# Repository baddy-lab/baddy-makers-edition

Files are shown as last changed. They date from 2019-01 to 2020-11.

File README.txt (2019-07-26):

    .__        ___       _______   _______  ____    ____
|   _  \      /   \     |       \ |       \ \   \  /   /
|  |_)  |    /  ^  \    |  .--.  ||  .--.  | \   \/   /
|   _  <    /  /_\  \   |  |  |  ||  |  |  |  \_    _/
|  |_)  |  /  _____  \  |  '--'  ||  '--'  |    |  |
|______/  /__/     \__\ |_______/ |_______/     |__|

Copyright Benoit GRESLEBIN 2018.
This documentation describes Open Hardware and is licensed under the
CERN OHL v. 1.1.  You may redistribute and modify this documentation
under the terms of the CERN OHL v.1.1. (http://ohwr.org/cernohl). This
documentation is distributed WITHOUT ANY EXPRESS OR IMPLIED WARRANTY,
INCLUDING OF MERCHANTABILITY, SATISFACTORY QUALITY AND FITNESS FOR A
PARTICULAR PURPOSE. Please see the CERN OHL v.1.1 for applicable conditions

######################################
ADDITIONAL TERMS
######################################
Specific non commercial use term: This source Hardware plan may be copied, distributed, modified by any individual
and non profit organizations (Fablab, Hackerspaces, Makerspaces, universities, Schools), as long
as it follows the CERN OHL V1.1 license terms here attached.
Corporate institutions and private companies may only copy and distribute the Hardware plan without modification.
Therefore, they are not allowed to modify the Hardware plan prior to distributing it for commercial purpose.
So for example, if a user embeds or modifies or relies on the Hardware plan in a product that is
then sold to a third party, this would be a violation of the Non-Commercial Use License additional term. 
By adding this additional restriction, it is intended to encourage the evolution of BADDY Hardware plan 
and design to be driven by the Hacker and makers' communities.

######################################
CONTRIBUTORS
######################################
Any change to be proposed on this gitlab, or at contact@baddy.space

######################################
PRODUCTS AND DISTRIBUTORS
######################################
Any intent of commercial use (selling BADDY Hardware DIY Kits and add-ons, not services around BADDY) to be notified to contact@baddy.space

######################################
CHANGE LOG - HISTORY
######################################

February 2018 - First open release
November 2018 - New git lab using Electrolab environment
January 2019 - New git public repository on GitHub

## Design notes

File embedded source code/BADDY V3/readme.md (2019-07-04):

In order to install BADDY new firmware, you need:
- To install VScode with PlatformIO modules installed. Once VS code installed, install the PlatformIO add-on with it's C/C++ extensions
- Take and Android cable (data transferred enabled) to connect your BADDY to your laptop (mac or PC)
- Note that OTA update available (to BADDY WiFi network) and uncomment the lines with ";" int the platformio.ini file.

The libraries that need to be installed:
- ArduinoJson by Benoit Blanchon
- LedControl by Eberhard Fahle
- AsyncTCP and ESPAsynTCP by Hristo Gochkov
- mDNSResolver by Myles Eftos

Once main.cpp, platformini.io and libraries installed and ready, please build project and upload and monitor to check logs

For any question, please join BADDY Facebook Group - there is a dedicated discussion Group on Firmware updates

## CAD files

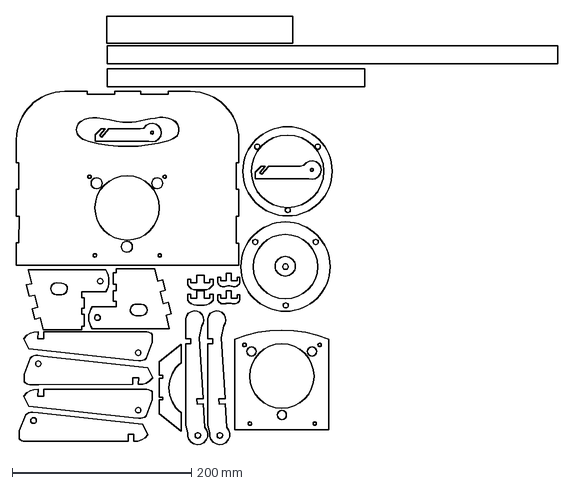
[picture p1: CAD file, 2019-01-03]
lasercut parts - mechanics and box/BADDY V1 DIY - 6mm.dxf
604.5 x 479.3 mm

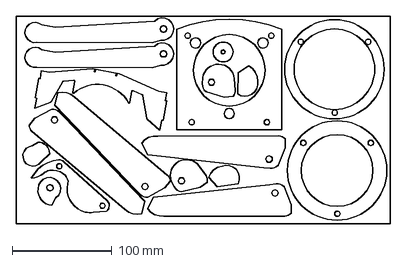
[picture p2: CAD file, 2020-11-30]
lasercut parts - mechanics and box/box v3/BADDY 6mm PMMA.dxf
375.2 x 207.9 mm

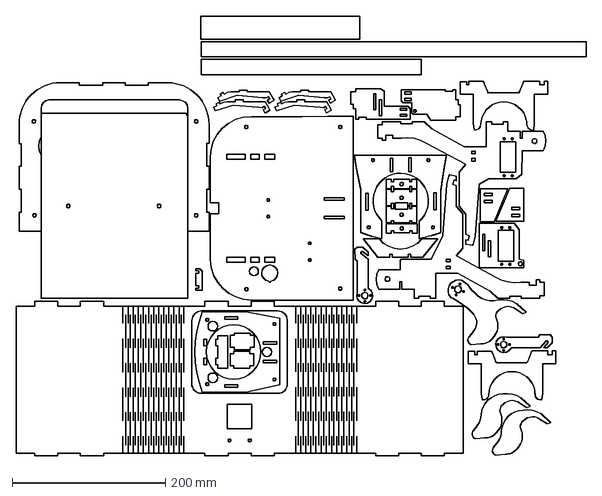
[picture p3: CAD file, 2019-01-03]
lasercut parts - mechanics and box/BADDY V1 DIY - 3mm.dxf
745.1 x 574.3 mm

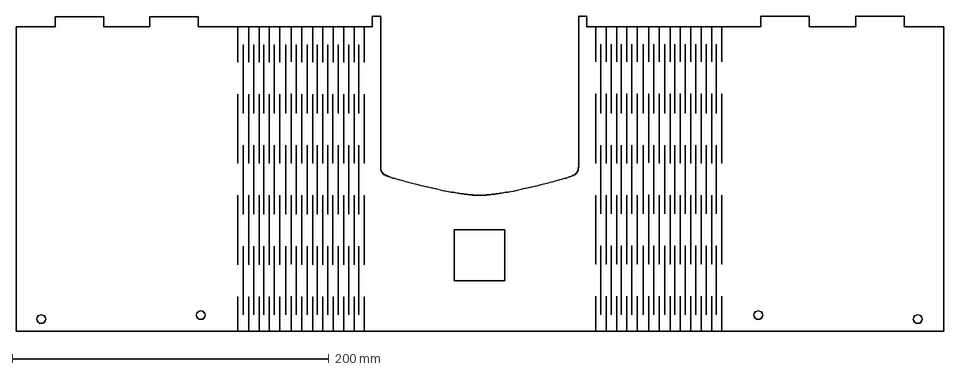
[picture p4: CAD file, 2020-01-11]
lasercut parts - mechanics and box/box v3/3mm front mdf.dxf
585.1 x 199.0 mm

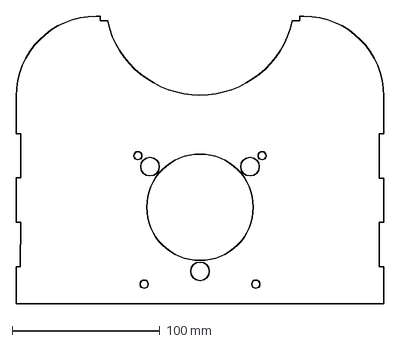
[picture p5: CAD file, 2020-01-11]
lasercut parts - mechanics and box/box v3/6mm top mdf.dxf
248.5 x 194.3 mm

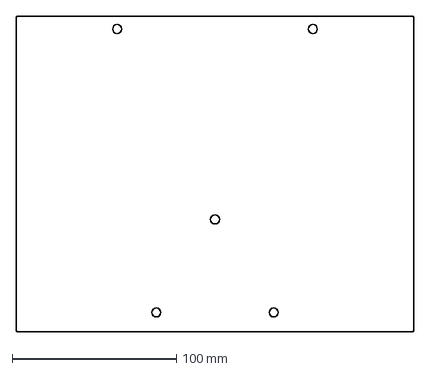
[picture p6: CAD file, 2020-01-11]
lasercut parts - mechanics and box/box v3/3mm back mdf.dxf
242.0 x 192.0 mm

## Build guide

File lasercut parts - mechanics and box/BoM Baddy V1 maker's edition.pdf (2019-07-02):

Groups | Mounting Steps | Video tutorial + Photo reference | Reference | Description | Quantity | Size | Comments
| 1 | | | Baddy box | 5 | | 5 units of glued wood or plexisglass
| | | BADDY BOX PL3 001 | Box front | 1
| | | BADDY BOX PL6 002 | Box top | 1
| | | BADDY BOX PL3 003 | Box bottom | 1
| | | BADDY BOX PL3 004 | Box lid | 1
| | | BADDY BOX PL6 005 | Box tube magnet cap | 1
| 2 | | | Baddy feeder | 3
| | | BADDY TUB PL3 006 | Tube | 1 | | Transparent tube diameter : 80 / 74mm ; height : 61 cm
| | | BADDY TUB PL6 007 | Tube lower collar | 1
| | | BADDY TUB PL6 008 | Tube upper collar | 1
| | | | Feeder screw | 3 | M6X18 | 3 Chc screwswith collar 6
| 3 | | | Baddy frame | 4 | | 4 glued units
| | | BADDY FRA PL3 009 | Frame lower board | 1
| | | BADDY FRA PL6 010 | Frame right side | 1
| | | BADDY FRA PL3 011 | Frame left side | 1
| | | BADDY FRA PL3 012 | Frame upper board | 1 | | In wood
| 4 | | | Baddy Firebox | 22 | | 22 glued units
| | | BADDY CHA PL3 013 | Firebox right side | 1
| | | BADDY CHA PL3 014 | Firebox left side | 1
| | | BADDY CHA PL3 015 | Firebox front assembly cleat | 1
| | | BADDY CHA PL3 016 | Firebox back cleat | 2
| | | BADDY CHA PL3 017 | Firebox upper board | 1
| | | BADDY CHA PL3 018 | Firebox magnet board | 1
| | | BADDY CHA PL3 019 | Firebox second right side | 1
| | | BADDY CHA PL3 020 | Firebox second left side | 1
| | | BADDY CHA PL6 021 | Firebox upper retainer neck | 1
| | | BADDY CHA PL3 022 | Firebox lower retainer neck | 1
| | | BADDY CHA PL3 023 | Firebox flange | 4
| | | BADDY CHA PL3 024 | Firebox wing | 2
| | | BADDY CHA PL3 025 | Firebox servo-motor board | 1
| | | BADDY CHA PL3 026 | Firebox spacer | 2
| | | BADDY CHA PL3 027 | Firebox servo-motor support | 1
| | | BADDY CHA PL3 028 | Firebox shuttle holder | 1
| 5 | | | Baddy shuttle retainer | 6 | | 3 glued units
| | | BADDY CHA PL3 029 | Firebox retainer | 2 | | 1 added part
| | | BADDY CHA PL3 030 | Firebox right arm | 2 | | 1 added part
| | | BADDY CHA PL6 031 | Firebox left arm | 2 | | 1 added part
| 6 | | | Baddy shuttle switch | 3 | | 3 glued units
| | | BADDY CHA PL3 032 | Firebox central switch | 1
| | | BADDY CHA PL3 033 | Firebox side switch | 2
| 7 | | | Front foot | 6 | | 6 glued units
| | | BADDY FRA PL6 034 | Baddy frame front foot | 4
| | | BADDY FRA PL6 035 | Baddy frame front foot cleat | 2
| | | | Rear foot | 5 | | 4 glued units
| | | BADDY FRA PL6 036 | Baddy frame rear foot | 2
| | | BADDY FRA PL6 037 | Baddy frame rear foot cleat | 2
| | | BADDY FRA PL6 038 | Baddy frame rear foot washer | 1 | | Thickness : 6 cm

BADDY
Structure

End of glued operations

Electronics +
Motors
8 | BADDY FRA 3D8 039 | Tripod holder | 1 | | 3D unit
| | Tripod holder bolt | 2 | M3x12 | 2 countersunk head screws + 2nylstop nuts
9 | BADDY CHA ELE 040 | Switch and retainer servo-motors | 2 | | H-KING HK 15298
| | Servo-motor bolt | 8 | M2,5x12 | 8 Chc screws + 8 nylstop nuts
10 | BADDY FRA ELE 041 | Motors | 2 | | 5,5V / 3A with ESC, beam and donkey
| | Motor bolt | 8 | M4x20 | 8 Chc screws + 8 nylstop nuts
| | Rubber washer | 16 | 4 – 9 | 16 ruber washers
| | Washer | 16 | 4 – 10 | 16 washers
11 | BADDY BOX ELE 042 | PCB 6 8X8 display beam (Led Square) | 1 | | 8X8 display – PCB card + 5 pinheader beam
| BADDY BOX WO3 043 | Baddy identity plate | 1 | | Fixed on Baddy box with 8X8 display
| | 8x8 display spacer | 2 | 3 – 7 – 6 | 2 spacers length : 6
| | 8x8 display bolt | 2 | M3x20 | 2 Chc screws + 2 nylstop nuts
12 | | Electronic card | 3 | | 2 units to pin on 1 Baddy PCB
| BADDY FRA ELE 044 | PCB card | 1
| BADDY FRA ELE 045 | Nano Arduino | 1 | | Pin on PCB card
| BADDY FRA ELE 046 | Bluetooth card | 1 | | Pin on PCB card
| | Electronic card spacer | 2 | 3 - 7 - 8 | 2 spacers length : 6
| | Electronic card bolt | 2 | M3x16 | 2 Chc screws + 2 nylstop nuts
13 | BADDY FRA ELE 047 | Switch on/off | 1 | | 1 unit to clip on Baddy lower frame
14 | BADDY FRA ELE 048 | Battery block | 1 | | PM-12V 6800mAh-CLIB ; battery beam to plug with main beam
15 | BADDY FRA ELE 049 | Main electric beam | 1 | | Motors - switch on/off – battery block
16 | | Assembly shuttle Firebox on Baddy frame front bolt | 1 | M4x20 | 1 Chc screw + 1 nylstop nut + 1 washer
Note: motor wire and servo-motors shall be wired to PCB Battery shall be connected to electric beam

Important: Before going to next step, please power on to initialize servo-motors position

Internal parts assembly | 17 | | Pulley on servo-motor | 2 | | Pulleys provided with servo-motors (drill 4 holes : 2 mm)
| | | Shuttle switch pulley bolt | 4 | M2x8 | 4 Chc screws + 4 nylstop nuts
| | | Shuttle retainer pulley bolt | 4 | M2x8 | 4 Chc screws + 4 nylstop nuts
| | | Shuttle retainer bolt on shuttle Firebox | 1 | M3x16 | 1 Chc screw + 1 nylstop nut + 3 washers
| | | Pulley on servo-motor screw | 2 | M3X7 | Provided with servo-motors
| 18 | BADDY FRA ELE 050 | Baddy wheel hub | 2 | | Assembly on wheels
| | | Wheel hub bolt | 8 | M3X10 | 8 Chc screws + 8 nylstop nuts
| | BADDY FRA ELE 051 | Baddy wheel | 2 | | Assembly on motors (allen key provided with the hub)
| 19 | BADDY BOX MAG 052 | Magnet | 3 | | Power : 10 daN
| 20 | | Assembly shuttle Firebox on Baddy box bolt | 4 | M3x25 | 4 Chc screws + 4 nylstop nuts
| 21 | | Assembly Baddy frame on Baddy box bolt | 4 | M4x12 | 4 Chc screws + 4 nylstop nuts

Connection 8X8 Led Square (Display Beam) to electronic card

End of assembly Baddy frame on Baddy box

External parts assembly | 22 | | Lid | 1 | | Assembly on shuttle firebox closing the Baddybox
| | | Rear lid pinched nut | 2 | | 2 pinched nuts
| | | Rear lid screw | 2 | M4x16 | 2 Chc screws
| | | Baddy box feet
| | | Front foot bolt | 2 | M6X30 | 2 Chc screws + 2 nylstop nuts + 12 washers
| | | Rear foot bolt | 1 | M6X34 | 1 Chc screw + 1 nylstop nut + 4 washers + rear foot washer 6cm
| 23 | BADDY BOX ELE 053 | USB cable | 1
| 24 | BADDY BOX TRI 054 | Tripod adapter | 1
| 25 | BADDY BOX ELE 055 | Battery charger | 1

## OPERATING BADDY

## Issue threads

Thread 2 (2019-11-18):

Wheels missing?

gistol, 2019-11-18:
Hi. Can you share some CAD files or .svg vector files for the wheels?

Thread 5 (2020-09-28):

Implicit assumptions

gvghia, 2020-09-28:
The program is full of assumptions and because they are not asserted, the controller can easily get into trouble.
The assumptions are that the positions to play are fixed and that there is a range of speeds attached to it.
The adjusting of motor speeds is based on these assumptions, which is so bad programming.
It is also limiting the uses of the Baddy.

What should be done in the speedadjuster is that the entered speeds are compared and not the programmed types. Based on the difference, some intermediate speed steps are to be done or not. For one step, the intermediate speed could be calculated as  the average of the actual running speed and the target speed. With a negative difference, you can decide to break or not, to reduce speed.

I'm talking about int motor_speed_transition(int type, int next_type){
From the types you get the programmed speeds: speed and next_speed for each motor.
With these  speeds you do the necessary adjustments by calling for each motor:
 int motor_speed_adjust(int motor, int speed, int next_speed){
if speed == next_speed return
if speed - next_speed > brake_step do_some_breaking(motor, speed, next_speed)
if next_speed - speed > acceleration_step do_some_acceleration(motor, speed, next_speed)
set_speed(motor, next_speed)
return

This simplifies the program a lot, because all type transistions use the same routine.

It will avoid unadapted speed transitions, when the implicit assumptions are not there.

Because the transistions are based on the required speeds, the speed adjustment is smoother.

It enlarge the possibilities in the training strokes of Baddy.
For example: we train youth players and operate Baddy, at the same side of the net as Baddy. As we face also the net, it is a mirrored view as the player who operates Baddy himself.
For easy programming, and having the same terrain view on the screen of the app, it makes sense to switch drop and clear by reversing the higher and lower speeds.
Also when I want the 9 training points on a line, or reduce the surface of the 9 point square to eg the backhand rear, or  ...
In both these cases, the controller is inducing contraproductive speed steps, which make these modes of operation almost impossible.

We are also looking out for more saved settings, (10?) in addition of the 2 existing, ground and tripod settings, preferably named, as we train also for Minibad, which uses only half of a field and therefore need settings to cover a narower surface.

baddy-team, 2020-11-11:
Hello! Thanks for reviewing the code. Yes, functions need to be updated, especially this one, that needs some cleaning and enables more dynamic configurability. We initially wanted something generic, but here comes the reality of the field experience, and in our context, these are 2 structuring points to bear in mind (among others not listed below), which led to this current versions with static exceptions:

- We cannot control Acceleration curves on ESCs, we just input speeds values to ESCs. That means we can't really control the time frame when an ESC will change from speed A to speed B
- We have to cope with batteries burst capabilities (ESCs may ask for 20A at full burst) which can block the battery

Given the 2 structuring points above, the situation is getting actually a bit more tricky than expected, and had finally to configure for each combination speed A to speed B, the most accurate speeds changes (mainly static considerations, yes).

That doesn't mean it's not possible to rewrite it, it's rather a must (like many other parts of BADDY code). But let's be careful to test it accurately before releasing anything, since this function actually impacts the functioning of the robot, in solo and buddy mode.

So, don't hesitate to push a proposal and I guess a lot of members will be glad to test and experience with you (we will thoroughly test any update before release).

We keep in touch!

gvghia, 2020-11-12:
Hi,

I want to suggest the varspeedservo [3] library.

Not tested myself, but it seems very easy to change the speeds in an
acceleration manner.
I think it will take some experiments to find an optimum between time
and current drawn.
It seems you can read back [4] the value and thus know if the speed
(programaticaly) is atteint.

I think this will simplify a lot the speed settings.

Other measures may be extended separate buffering of the 12v supply to
the Arduino. (eg 12 V - 10 ohm - 5000 uF - supply Arduino)

Another suggestion is a function that the front display indicates the
positon of the next trow.  Of course it is switchable, so random can
still be unexpected!

Regards,

Gerard Vanderveken

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

Links:
------
[1]
https://github.com/baddy-lab/baddy-makers-edition/issues/5#issuecomment-725653972
[2]
https://github.com/notifications/unsubscribe-auth/AGV7GXCZ6V2QJEIFL4AZF7DSPL2G3ANCNFSM4R4JFUMA
[3] https://forum.arduino.cc/index.php?topic=61586.0
[4] https://forum.arduino.cc/index.php?topic=68305.msg504226#msg504226

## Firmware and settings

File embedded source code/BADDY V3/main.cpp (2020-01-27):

/*
        .__        ___       _______   _______  ____    ____
    |   _  \      /   \     |       \ |       \ \   \  /   /
    |  |_)  |    /  ^  \    |  .--.  ||  .--.  | \   \/   /
    |   _  <    /  /_\  \   |  |  |  ||  |  |  |  \_    _/
    |  |_)  |  /  _____  \  |  '--'  ||  '--'  |    |  |
    |______/  /__/     \__\ |_______/ |_______/     |__|


    ###########################################################################
    BADDY_EMBEDDED_CODE_ESP_V01.ino - Embedded source code of BADDY ESP (wifi version)
    Copyright (C) 2017  GRESLEBIN Benoit
    ###########################################################################

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
    ######################################
    ADDITIONAL TERMS
    ######################################
    Specific non commercial use term: This source code may be copied, distributed, modified by any individual
    and non profit organizations (Fablab, Hackerspaces, Makerspaces, universities, Schools), as long
    as it follows the GNU GPL license terms here attached.
    Corporate institutions and private companies may only copy and distribute the source code without modification.
    Therefore, they are not allowed to modify the source code prior to distributing it for commercial purpose.
    So for example, if a user embeds or modifies or relies on the source code in a product that is
    then sold to a third party, this would be a violation of the Non-Commercial Use License
    additional term, although this type of use would be permitted under the standard GNU GPL
    (assuming the other terms and conditions of the GNU GPL v.3 were followed). By adding this additional
    restriction, it is intended to encourage the evolution of BADDY source code to be driven
    by the Hacker and makers' communities.

    ######################################
    COPYRIGHT NOTICE
    ######################################
    LedControl.h is a software library under MIT license, Copyright (c) 2007-2015 Eberhard Fahle
    ArduinoJson.h is a software library, Copyright (c) Benoit Blanchon
    ESPAsyncWebServer.h and ESPAsyncTCP.h are software libraries, Copyright (c) by Hristo Gochkov

    ######################################
    HISTORY
    ######################################
    May 2018 - ESP based code (wifi version), using aRest library, but not a final choice
    July 2018 - BUDDY feature implemented (connect 2 BADDY), get rid of aRest library, implemented simple webserver instead
    Sep 2018 - Async implementation to make sure server interrupts are taken into account without delay by BADDY
    Dec 2018 - Battery level management, taking into account latest battery level management
    Jan 2019 - Change acceleration settings to prevent triggering battery protect feature. Update transition_speed() method between drop shots
    June 2019 - Firmware v2.0.1 / hot spot connection, compatibility with GO BADDY app V3
    July 2019 - Firmware v2.0.5 / updates on BUDDY mode control
    Jan 2020 - optimization and fixes for BUDDY synchro issues. Activation of All you can eat feature for BUDDY mode
*/

#include <Arduino.h>
#include <LedControl.h>
#include <ESP8266WiFi.h>
#include <Servo.h>
#include <ArduinoJson.h>
#include "FS.h"
#include <ESP8266HTTPClient.h>
#include <ESPAsyncTCP.h>
#include <ESPAsyncWebServer.h>
#include <ESP8266mDNS.h>
#include <mDNSResolver.h>
#include <WiFiClient.h>
#include <WiFiUdp.h>
#include <ArduinoOTA.h>

// ESP Pin configurations

#define LED_DIN D2
#define LED_CS D1
#define LED_CLK D3
#define MOTOR_RIGHT_PIN D5
#define MOTOR_LEFT_PIN D7
#define SHUTTLE_SWITCH_PIN D6
#define SHUTTLE_RETAINER_PIN D8
//In case you want to use the EXT pin header for your Retainer servo motor, comment the line above and uncomment the line just below
// #define SHUTTLE_RETAINER_PIN D0
#define ANALOG_READ_BATTERY A0

// ESP Pin configurations end

String baddy_firmware_version = "2.0.7";

String connect_mode = "";
bool flag_new_sequence = false;
bool station_connected = false;
bool buddy_around = false;
String JsonSequence;

//Wifi related static values for BADDY as a server
const char *BADDY_ID = "BADDY-V2"; // Usually CCDDD where CC is your country and DDD is a 3 digit number between 000 and 999
String ssid; // Keep "BADDY-" and add your BADDY ID at the end
const char *ssid_init = "BADDY";
const char *password_init = "";
String password;

using namespace mDNSResolver;
WiFiUDP udp;
Resolver resolver(udp);
IPAddress BaddyMasterIP (0, 0, 0, 0); // This is BADDY master's address when BUDDY mode
String buddy_ip_address;

// Those are the addresses when BADDY in AP/Wifi access point mode (happens when BADDY can't connect on Hot spot/Client mode)
IPAddress baddy_ip(192,168,1,2);
IPAddress baddy_gateway(192,168,1,1);
IPAddress baddy_subnet(255,255,255,0);

// BADDY BUDDY server related parameters
const uint16_t port = 80;
const char * host = "192.168.4.2"; // ip or dns
HTTPClient buddy;
WiFiClient client_buddy;

// Wifi event handler functions

WiFiEventHandler stationConnectedHandler;
WiFiEventHandler stationDisconnectedHandler;


// Wifi event handler functions end

// Wifi related static values end

// Create an instance of the server
AsyncWebServer server(80);

/////////////////////////////JSON DOCUMENT FORMAT//////////////////////////////////
/*
{
    "Type": "SEQ",
    "Strokes": [ 1, 1, 2, 3, 4, 5, 6, 7, 8, 9, 1, 11, 12, 13, 14, 15, 16, 17, 18, 19, 2 ],
    "Speeds": [ 1, 1, 2, 3, 4, 5, 6, 7, 8, 9, 1, 1, 2, 3, 4, 5, 6, 7, 8, 9 , 1],
    "LoopMode": 0
}*/
    // For testing purpose
   // char json[] = "{\"Type\":\"SEQ\",\"Strokes\": [ 0, 1, 2, 3, 4, 5, 6, 7, 8, 9, 10, 11, 12, 13, 14, 15, 16, 17, 18, 19, 20 ],\"Speeds\": [ 0, 1, 2, 3, 4, 5, 6, 7, 8, 9, 10, 1, 2, 3, 4, 5, 6, 7, 8, 9 , 10],\"LoopMode\": 0}";
    // Computed with Arduino Json assistant

//Json Object values:
String type_seq;
int stroke_seq[20];
int stroke_seq_buddy[20];
int speed_seq[20];
int speed_seq_buddy[20];
int loop_mode_seq;
int PlayMode = 0;
int i; //integer that parses the sequence int Array. We make a global value to manage it in the main loop()
int speed;
int flag_first_shot=1;
int random_id; // used in random loop
int random_id_next; //used in random_loop
int stroke_count=0; //used in random loop
String json_config; // Needed to expose variable to Rest API
String json_status;
String json_playmode_dump;
bool flag_test_shot = 0;
bool all_you_can_eat_flag = 0;

bool running_status = false; // boolean flag that indicates if BADDY running or stopped (motors don't spin), initialized with 0
int battery_level;     // Battery level management

/////////////////////////////JSON DOCUMENT FORMAT END//////////////////////////////

/////////////////////////////Statistics counter and functions//////////////////////////////

int COUNTER_DROP_LEFT = 0;
int COUNTER_DROP_CENTER = 0;
int COUNTER_DROP_RIGHT = 0;
int COUNTER_DRIVE_LEFT = 0;
int COUNTER_DRIVE_CENTER = 0;
int COUNTER_DRIVE_RIGHT = 0;
int COUNTER_CLEAR_LEFT = 0;
int COUNTER_CLEAR_CENTER = 0;
int COUNTER_CLEAR_RIGHT = 0;

void reset_stats_counter()
{
    Serial.println("Reset stats counter... ");
    COUNTER_DROP_LEFT = 0;
    COUNTER_DROP_CENTER = 0;
    COUNTER_DROP_RIGHT = 0;
    COUNTER_DRIVE_LEFT = 0;
    COUNTER_DRIVE_CENTER = 0;
    COUNTER_DRIVE_RIGHT = 0;
    COUNTER_CLEAR_LEFT = 0;
    COUNTER_CLEAR_CENTER = 0;
    COUNTER_CLEAR_RIGHT = 0;
}

/////////////////////////////Statistics counter END//////////////////////////////

///////////////////////////////////////////////////////////////////////////////////
/////////////////////////////CONFIGURATION PARAMETERS - FACTORY SETTINGS //////////////////////////////
///////////////////////////////////////////////////////////////////////////////////

//Warm up, break timer, stop speed, computation timer - modify only if you know what you are doing
int WARM_UP_SPEED=890;
int TRANSITION_SPEED=875;
int TRANSITION_SPEED_HIGH = 990;
int STOP = 750;
int WARM_UP_TIMER = 2000;
int COMPUTATION_TIMER = 600;
int BREAK_TIMER = 500;
int BUDDY_TIMER = 700; // Timer to synchronize BADDY and BUDDY

// DROP SHOTS
int DROP_LEFT_SHOT_LEFT_MOTOR=910;//950;
int DROP_LEFT_SHOT_RIGHT_MOTOR=843;//860;
int DROP_CENTER_SHOT_LEFT_MOTOR=845;//880;
int DROP_CENTER_SHOT_RIGHT_MOTOR=845;//880;
int DROP_RIGHT_SHOT_LEFT_MOTOR=840;//860;
int DROP_RIGHT_SHOT_RIGHT_MOTOR=910;//950;
//DRIVE SHOTS
int DRIVE_LEFT_SHOT_LEFT_MOTOR=1050;
int DRIVE_LEFT_SHOT_RIGHT_MOTOR=875;
int DRIVE_CENTER_SHOT_LEFT_MOTOR=990;
int DRIVE_CENTER_SHOT_RIGHT_MOTOR=990;
int DRIVE_RIGHT_SHOT_LEFT_MOTOR=875;
int DRIVE_RIGHT_SHOT_RIGHT_MOTOR=1050;
//CLEAR SHOTS
int CLEAR_LEFT_SHOT_LEFT_MOTOR=1300;
int CLEAR_LEFT_SHOT_RIGHT_MOTOR=930;
int CLEAR_CENTER_SHOT_LEFT_MOTOR=1350;
int CLEAR_CENTER_SHOT_RIGHT_MOTOR=1350;
int CLEAR_RIGHT_SHOT_LEFT_MOTOR=930;
int CLEAR_RIGHT_SHOT_RIGHT_MOTOR=1300;

//Switch movement and timers
int SWITCH_LONG_POSITION = 75;
int SWITCH_SHORT_POSITION = 140;
int SWITCH_WAIT_POSITION = 90;
int SWITCH_TIMER = 300;//320 // value in millisecond to wait Switch to fetch its long position
int SWITCH_SPEED=600; // Special speed for slow motion movement (configuration)

// Shuttle retainer movemement and timers
int RETAINER_UP_POSITION = 115;
int RETAINER_DOWN_POSITION = 158;
int RETAINER_TIMER = 160;//150

//Network profile init parameters
const char* network_init_ssid = "BADDY-init";
const char* network_init_pwd = "BADDY1234";

// Use at Json config object creation
int SpeedProfileInit[18] =      {DROP_LEFT_SHOT_LEFT_MOTOR, DROP_LEFT_SHOT_RIGHT_MOTOR, DROP_CENTER_SHOT_LEFT_MOTOR, DROP_CENTER_SHOT_RIGHT_MOTOR, DROP_RIGHT_SHOT_LEFT_MOTOR, DROP_RIGHT_SHOT_RIGHT_MOTOR, DRIVE_LEFT_SHOT_LEFT_MOTOR, DRIVE_LEFT_SHOT_RIGHT_MOTOR, DRIVE_CENTER_SHOT_LEFT_MOTOR, DRIVE_CENTER_SHOT_RIGHT_MOTOR, DRIVE_RIGHT_SHOT_LEFT_MOTOR, DRIVE_RIGHT_SHOT_RIGHT_MOTOR, CLEAR_LEFT_SHOT_LEFT_MOTOR, CLEAR_LEFT_SHOT_RIGHT_MOTOR, CLEAR_CENTER_SHOT_LEFT_MOTOR, CLEAR_CENTER_SHOT_RIGHT_MOTOR, CLEAR_RIGHT_SHOT_LEFT_MOTOR, CLEAR_RIGHT_SHOT_RIGHT_MOTOR};
int SwitchProfileInit[2]=     {SWITCH_LONG_POSITION, SWITCH_SHORT_POSITION};
int RetainerProfileInit[2]=     {RETAINER_UP_POSITION, RETAINER_DOWN_POSITION};

// Servos instances

Servo ShuttleRetainer;
Servo ShuttleSwitch;
Servo MotorLeft;
Servo MotorRight;

// Servo instances End

// Servo functions

void servo_fire(){

ShuttleRetainer.write(RETAINER_UP_POSITION);
delay(RETAINER_TIMER);

ShuttleSwitch.write(SWITCH_LONG_POSITION);
delay(SWITCH_TIMER);

ShuttleSwitch.write(SWITCH_SHORT_POSITION);
delay(SWITCH_TIMER);
ShuttleRetainer.write(RETAINER_DOWN_POSITION);

delay(RETAINER_TIMER); // Just in case

}

// Servo functions end

void dump_play_mode() {

    // JSON Object for Playmode dump
    DynamicJsonBuffer jsonPlaymode;
    JsonObject& PlayModeDump = jsonPlaymode.createObject();

    JsonArray& CurrentSpeeds = PlayModeDump.createNestedArray("CurrentSpeeds");
    PlayModeDump["PlayMode"] = PlayMode;

    CurrentSpeeds.add(DROP_LEFT_SHOT_LEFT_MOTOR);
    CurrentSpeeds.add(DROP_LEFT_SHOT_RIGHT_MOTOR);
    CurrentSpeeds.add(DROP_CENTER_SHOT_LEFT_MOTOR);
    CurrentSpeeds.add(DROP_CENTER_SHOT_RIGHT_MOTOR);
    CurrentSpeeds.add(DROP_RIGHT_SHOT_LEFT_MOTOR);
    CurrentSpeeds.add(DROP_RIGHT_SHOT_RIGHT_MOTOR);
    CurrentSpeeds.add(DRIVE_LEFT_SHOT_LEFT_MOTOR);
    CurrentSpeeds.add(DRIVE_LEFT_SHOT_RIGHT_MOTOR);
    CurrentSpeeds.add(DRIVE_CENTER_SHOT_LEFT_MOTOR);
    CurrentSpeeds.add(DRIVE_CENTER_SHOT_RIGHT_MOTOR);
    CurrentSpeeds.add(DRIVE_RIGHT_SHOT_LEFT_MOTOR);
    CurrentSpeeds.add(DRIVE_RIGHT_SHOT_RIGHT_MOTOR);
    CurrentSpeeds.add(CLEAR_LEFT_SHOT_LEFT_MOTOR);
    CurrentSpeeds.add(CLEAR_LEFT_SHOT_RIGHT_MOTOR);
    CurrentSpeeds.add(CLEAR_CENTER_SHOT_LEFT_MOTOR);
    CurrentSpeeds.add(CLEAR_CENTER_SHOT_RIGHT_MOTOR);
    CurrentSpeeds.add(CLEAR_RIGHT_SHOT_LEFT_MOTOR);
    CurrentSpeeds.add(CLEAR_RIGHT_SHOT_RIGHT_MOTOR);

    json_playmode_dump = ""; //empty first
    PlayModeDump.printTo(json_playmode_dump);
}

bool format_file_system_spifs() {
    // We format the file system
    SPIFFS.format();

    // JSON Object for BADDY configuration
    DynamicJsonBuffer jsonConfig;
    JsonObject& Config = jsonConfig.createObject();

    JsonArray& SpeedProfile = Config.createNestedArray("SpeedProfile");
    JsonArray& SpeedfloorProfile = Config.createNestedArray("SpeedfloorProfile");
    JsonArray& SpeedbuddyProfile = Config.createNestedArray("SpeedbuddyProfile");
    JsonArray& RetainerProfile = Config.createNestedArray("RetainerProfile");
    JsonArray& SwitchProfile = Config.createNestedArray("SwitchProfile");

    // We implement Config file with factory settings
    int index;

    for(index=0;index<18;index++)
    {
        SpeedProfile.add(SpeedProfileInit[index]);
        SpeedfloorProfile.add(SpeedProfileInit[index]);
        SpeedbuddyProfile.add(SpeedProfileInit[index]);
        /*Serial.print("Speed profile index value: ");
        Serial.print(index);
        Serial.print(", Speed profile index value: ");
        Serial.println(SpeedProfileInit[index]);
        */
    }

    for(index=0;index<2;index++)
    {
        RetainerProfile.add(RetainerProfileInit[index]);
        /*
        Serial.print("Retainer profile index value: ");
        Serial.print(index);
        Serial.print(", Retainer profile index value: ");
        Serial.println(RetainerProfileInit[index]);
        */
    }

    for(index=0;index<2;index++)
    {
        SwitchProfile.add(SwitchProfileInit[index]);
        /*
        Serial.print("Switch profile index value: ");
        Serial.print(index);
        Serial.print(", Switch profile index value: ");
        Serial.println(SwitchProfileInit[index]);
        */
    }

    Serial.println("Config object print before save to config file");
    //Config.prettyPrintTo(Serial);
    json_config = ""; // clean before print
    Config.printTo(json_config); // Saving global variable exposed to API

    // Saving into file system
    // We open a brand new file
    File file = SPIFFS.open("/BADDY_CONFIG_FILE", "w"); // Open BADDY config file
    Config.printTo(file); // Export and save JSON object to SPIFFS
    Serial.println("configuration saved to File system: ");
    //Config.prettyPrintTo(Serial);
    file.close();

    File file2 = SPIFFS.open("/BADDY_NET_FILE", "w"); // Open BADDY config file
    file2.print(network_init_ssid);
    file2.print('\n');
    file2.print(network_init_pwd);
    file2.print('\n');
    Serial.println("Network configuration saved to File system: ");
    file2.close();

    PlayMode = 0; // set to default if not already the case
    dump_play_mode(); // expose current playmode
    return 1;
}

bool set_network(const char* ssid_input, const char* password_input)
{
    Serial.println("Set_network end point triggered...");

    Serial.print("New ssid: ");
    Serial.println(ssid_input);
    Serial.print("New password: ");
    Serial.println(password_input);

    // We fetch data from file system
    File file = SPIFFS.open("/BADDY_NET_FILE", "r");

    if (!file){

        Serial.println("No BADDY network file exists");
        file.close();
        format_file_system_spifs();
        return false;

    }
    else {

        size_t size = file.size();
        if ( size == 0 ) {
            Serial.println("Config file empty !");
            file.close();
            //format_file_system();
            return false;
        }
        else {

            String read = file.readStringUntil('\n');
            Serial.println(read);
            read = file.readStringUntil('\n');
            Serial.println(read);            

            file.close();

            File file = SPIFFS.open("/BADDY_NET_FILE", "w");
            file.flush();

            // Now writing...
            file.print(ssid_input);
            file.print('\n');
            file.print(password_input);
            file.print('\n');
            Serial.println("Network configuration saved to File system: ");
            
        }

    file.close();
    return true;

    }
}
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
void loop() {

    //ArduinoOTA.handle();

    MDNS.update();

    if (flag_new_sequence)
    {
        sequencefetch(JsonSequence);
        ReadSequence();
    }

    if (flag_test_shot)
    {
        delay(1500);// wait till motors get their nominal speed
        Serial.println("Shooting shuttlecock...");
        servo_fire();
        flag_test_shot = 0;
        MotorRight.writeMicroseconds(STOP);
        MotorLeft.writeMicroseconds(STOP);
        Serial.println("Stop motors!");
    }

    if (flag_print_smiley)
    {
        printSmiley();
        flag_print_smiley = 0;
    }
    if (flag_print_frown)
    {
        printFrown();
        flag_print_frown = 0;
    }
    if (flag_print_squares)
    {
        printSquares();
        flag_print_squares = 0;
    }

}

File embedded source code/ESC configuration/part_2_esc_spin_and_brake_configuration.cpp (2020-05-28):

/*
  ____            _     _         ______  _____  _____                                                                 
 |  _ \          | |   | |       |  ____|/ ____|/ ____|                                                                
 | |_) | __ _  __| | __| |_   _  | |__  | (___ | |       _ __  _ __ ___   __ _ _ __ __ _ _ __ ___  _ __ ___   ___ _ __ 
 |  _ < / _` |/ _` |/ _` | | | | |  __|  \___ \| |      | '_ \| '__/ _ \ / _` | '__/ _` | '_ ` _ \| '_ ` _ \ / _ \ '__|
 | |_) | (_| | (_| | (_| | |_| | | |____ ____) | |____  | |_) | | | (_) | (_| | | | (_| | | | | | | | | | | |  __/ |   
 |____/ \__,_|\__,_|\__,_|\__, | |______|_____/ \_____| | .__/|_|  \___/ \__, |_|  \__,_|_| |_| |_|_| |_| |_|\___|_|   
                           __/ |                        | |               __/ |                                        
                          |___/                         |_|              |___/                                         
###########################################################################
    BADDY_EMBEDDED_CODE_ARDUINO_V01.ino - Embedded source code of BADDY Arduino working with bluetooth
    Copyright (C) 2016  GRESLEBIN Benoit
    ###########################################################################
    This program is free software: you can redistribute it and/or modify
    it under the terms of the GNU Affero General Public License as published by
    the Free Software Foundation, either version 3 of the License, or any later version.
    This program is distributed in the hope that it will be useful,
    but WITHOUT ANY WARRANTY; without even the implied warranty of
    MERCHANTABILITY or FITNESS FOR A PARTICULAR PURPOSE.  See the
    GNU Affero General Public License for more details.
    You should have received a copy of the GNU Affero General Public License
    along with this program.  If not, see <https://www.gnu.org/licenses/>.
    ######################################
    ADDITIONAL TERMS
    ######################################
    Specific non commercial use term: This source code may be copied, distributed, modified by any individual 
    and non profit organizations (Fablab, Hackerspaces, Makerspaces, universities, Schools), as long
    as it follows the GNU GPL license terms here attached.
    Corporate institutions and private companies may only copy and distribute the source code without modification.
    Therefore, they are not allowed to modify the source code prior to distributing it for commercial purpose.
    So for example, if a user embeds or modifies or relies on the source code in a product that is 
    then sold to a third party, this would be a violation of the Non-Commercial Use License 
    additional term, although this type of use would be permitted under the standard GNU GPL
    (assuming the other terms and conditions of the GNU GPL v.3 were followed). By adding this additional 
    restriction, it is intended to encourage the evolution of BADDY source code to be driven
    by the Hacker and makers' communities.
    ######################################
    History
    ######################################
    First Release: Alexander Secret (alex[at]baddy.space) (karolalexandersecret[at]gmail.com)

    ######################################
    How to use
    ######################################
    1 Select the right board: NodeMCU 0.9 (ESP-12 Module).
    2 Programm and download
    3 Open a terminal (115200 bauds).
    4 Follow the instuction :)
*/
#include <Arduino.h>
#include <Servo.h>
#include <ESP8266WiFi.h>

#define MOTOR_RIGHT_PIN_1 D5
#define MOTOR_LEFT_PIN_1 D7
#define samplerate 6000 
#define FPM_SLEEP_MAX_TIME 0xFFFFFFF

void WiFiOff();
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

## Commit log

2019-01-07 Add files via upload
    This code allows to configure your ESC (Electronic Speed Controllers), using your BADDY V2 electronics.
    Once done, please upload BADDY V2 code again to make your BADDY work as before ;)
2019-02-01 Update BADDY_V2_WIFI_EMBEDDED_CODE_ARDUINO_V01.ino
    Optimise timing between strokes (regression from battery protection fix)
    [BADDY_V2_WIFI_EMBEDDED_CODE_ARDUINO_V01.ino]
2019-07-02 BoM + mounting steps and screws set
2020-01-11 Make your BADDY Box V2
    Recommended raw material: wood or PMMA thickness 3mm and 6mm
    [3mm back mdf.dxf, 3mm front mdf.dxf, 6mm top mdf.dxf]
2020-01-27 2.0.7 update
    Mainly BUDDY mode fixes and improvements (remove synchro issue for complex sequences, remove synchro issue when shots in the middle of the court).
    Enablement of all you can eat feature (2 BUDDY shot a highest frequency).
    [main.cpp]
2020-05-28 Update Baddy V2_ESC_Programmer_ESP8266.ino
    Highlighting only the ESC configuration, ESC max and min put in comment
2020-07-15 Update platformio.ini
    Forcing Ledcontrol version to 1.0.6, as interface breach with more recent versions, leading to compilation errors.
2020-11-16 Rename embedded source code/Baddy V2_ESC_Programmer_ESP8266.ino to embedded source code/ESC configuration/ESC spin and brake configuration
2020-11-16 Rename ESC spin and brake configuration to part_2_esc_spin_and_brake_configuration.cpp
